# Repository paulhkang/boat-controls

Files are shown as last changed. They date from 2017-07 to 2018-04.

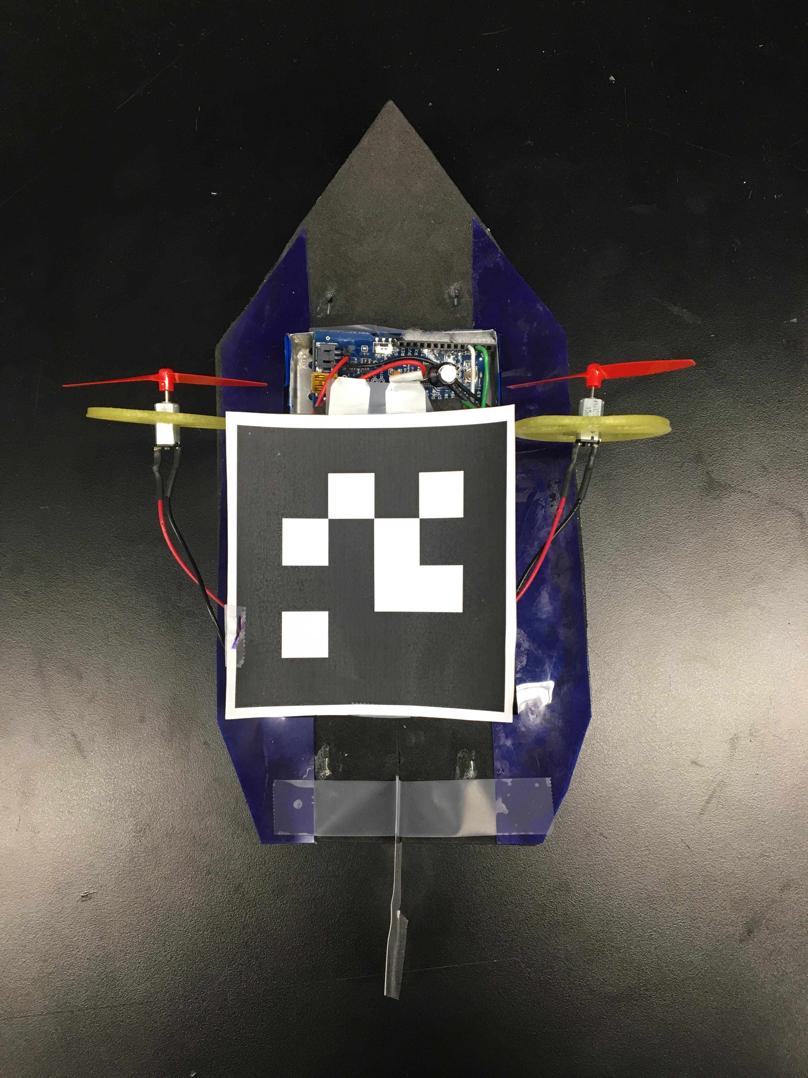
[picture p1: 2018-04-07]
Boat_Assembly/Photos/jack_boat_001.jpg

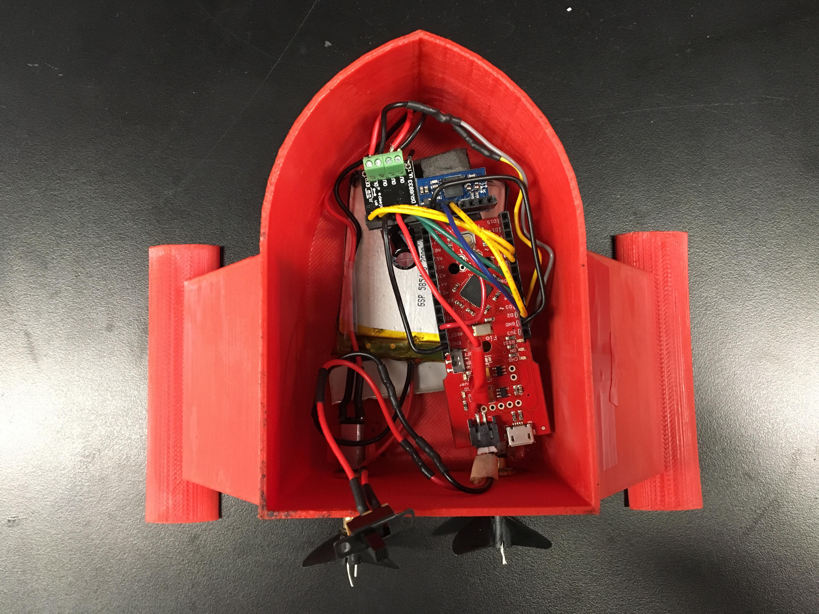
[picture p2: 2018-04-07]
Boat_Assembly/Photos/paul_boat_001.jpg

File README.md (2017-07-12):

# boat-controls
Controls for an Autonomous Boat

This repository contains the code for a control system on an autonomous boat.

The two contributors to this repository are Paul Kang and Rayhan Syed.
We are students at The Cooper Union, located in New York City.

The bno055.c and bno055.h files are used in reading from the Bosch Sensortec BNO055 sensor.
These files, as well as more detailed documentation on the software, can be found at: https://github.com/BoschSensortec/BNO055_driver.

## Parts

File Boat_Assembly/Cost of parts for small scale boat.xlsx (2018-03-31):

Part Name | Quantity | Cost | Link
P14350-ND motors | 2 | $4.11 | https://www.digikey.com/product-detail/en/nmb-technologies-corporation/PNN7RE08JD/P14350-ND/2417074
Arduino Fio | 1 | $24.95 | https://www.sparkfun.com/products/11520
Custom Arduino boards | 1 | $61.85 | X | (designed by Andrey Akhmetov, EE '20)
Li-Ion flat battery | 2 | 12.95 | https://www.sparkfun.com/products/8483
3D filament | As needed for testing
RC boat propellers | 3 (only 2 needed) | $7.98 | http://a.co/iIR0y6P
Total |  | $111.84
Non-costed parts:
Li-ion battery charger | 1
Brass motor shafts | 2 | Machined in-house (Sinisa Janjusevic)
Brass bearings | 2 | Machined in-house (Sinisa Janjusevic)
Vaseline for lubrication | N/A
Xbee S1 radio | 2 | https://www.sparkfun.com/products/8665
SparkFun Xbee Explorer Dongle | 1 | https://www.sparkfun.com/products/11697
Micro USB Cable (for writing to Arduino) | 1
Wire | N/A
Hot glue | N/A

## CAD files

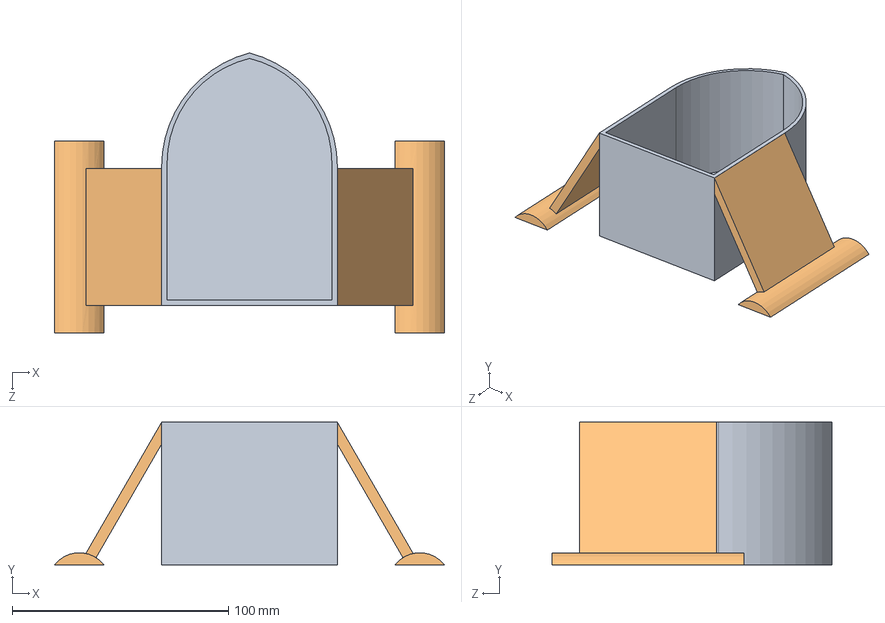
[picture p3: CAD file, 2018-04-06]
Boat_Assembly/CAD & Drawings/Boat Hull Assembly.SLDASM
180.3 x 66.0 x 129.5 mm
Boat Body
Boat Arm x 2

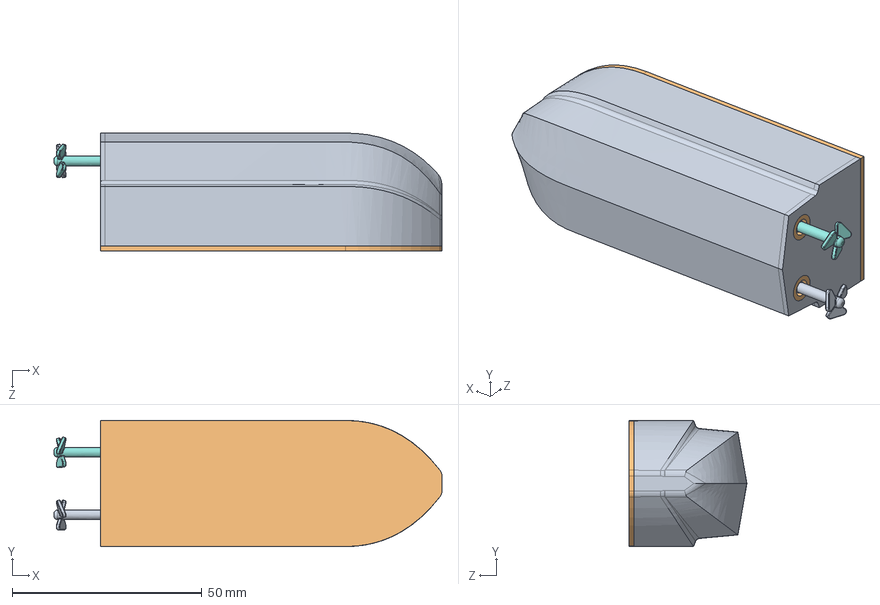
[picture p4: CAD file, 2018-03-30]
Boat_Assembly/TankData/mASV_CAD/dumb_boat.SLDASM
102.4 x 33.3 x 31.1 mm
hull
grommet x 2
battery_400mAh
miniBoard
XBee
minimotor_0615NS_sld x 2
minimotor_gearbox_4to1 x 2
propeller_LH
propeller_RH
cap

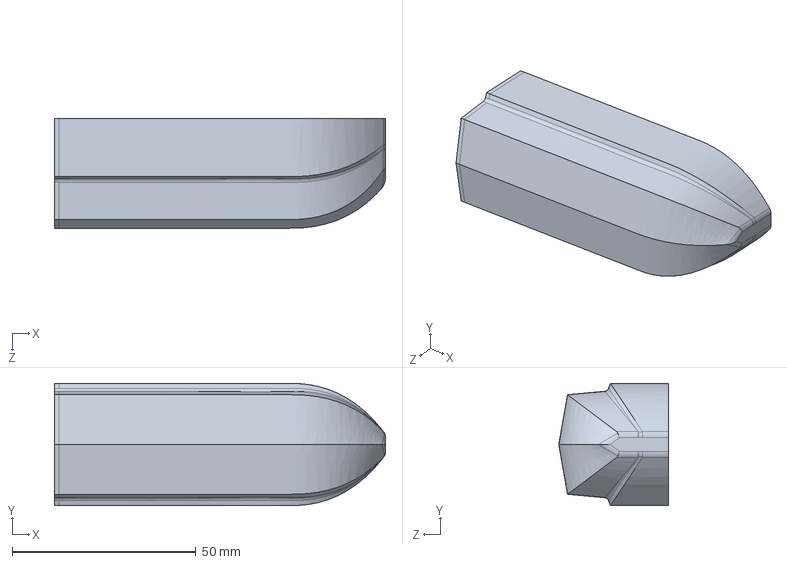
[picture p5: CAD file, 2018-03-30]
Boat_Assembly/TankData/mASV_CAD/hull.SLDPRT
90.2 x 33.3 x 29.8 mm

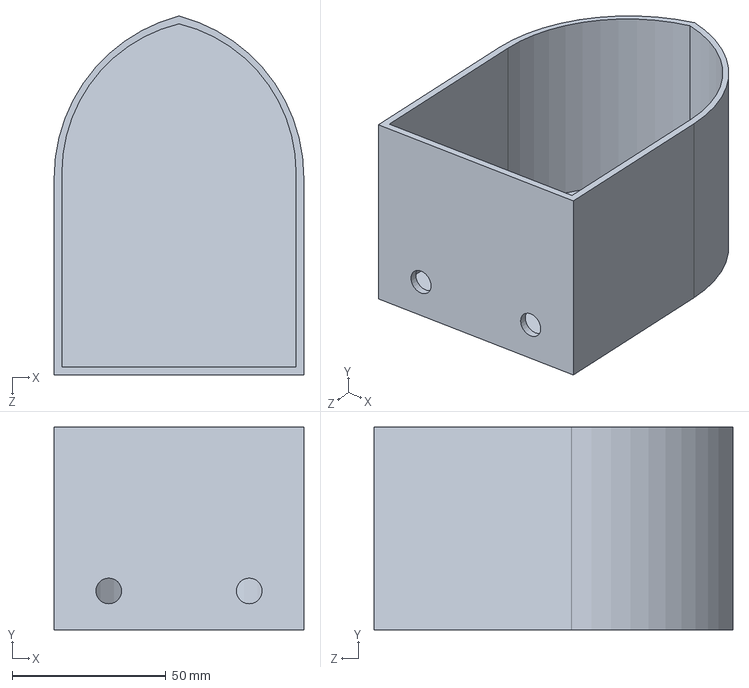
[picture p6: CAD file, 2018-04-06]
Boat_Assembly/CAD & Drawings/Boat Body.SLDPRT
81.3 x 66.0 x 116.8 mm

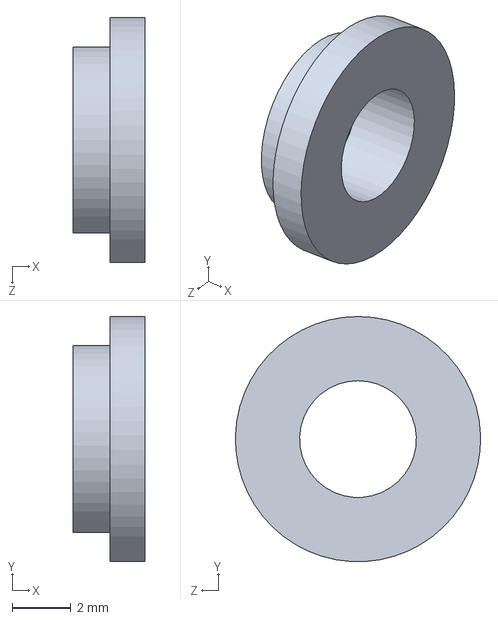
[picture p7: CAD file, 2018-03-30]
Boat_Assembly/TankData/mASV_CAD/grommet.SLDPRT
2.46 x 8.33 x 8.33 mm

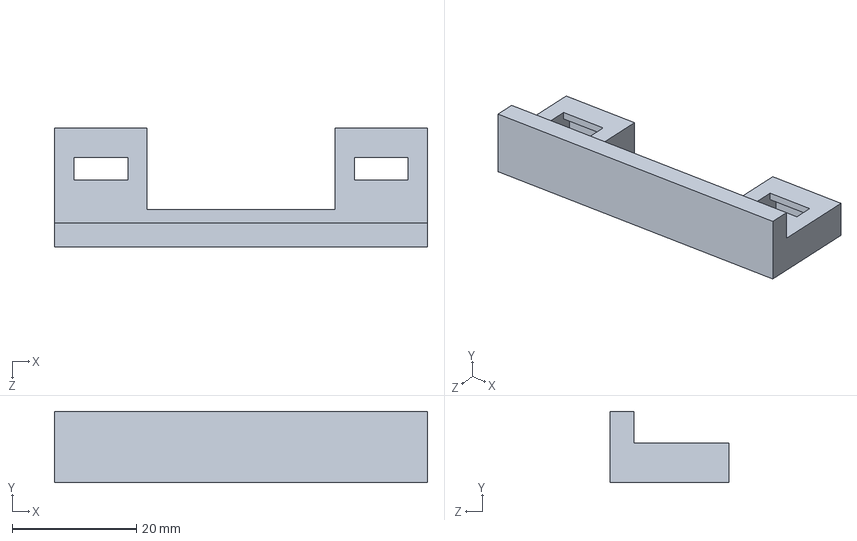
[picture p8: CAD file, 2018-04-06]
Boat_Assembly/CAD & Drawings/motor-mount.SLDPRT
59.9 x 11.4 x 19.0 mm

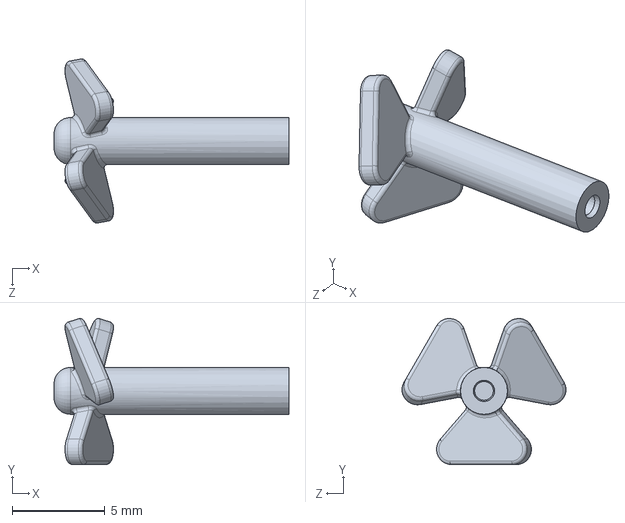
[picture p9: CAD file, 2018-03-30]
Boat_Assembly/TankData/mASV_CAD/propeller_RH.SLDPRT
12.7 x 7.89 x 8.87 mm

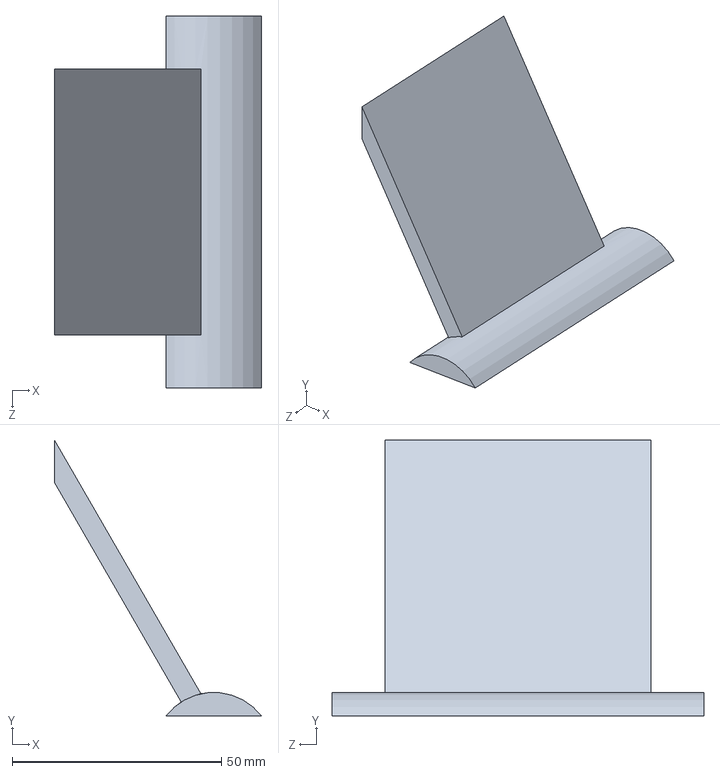
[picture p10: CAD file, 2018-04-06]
Boat_Assembly/CAD & Drawings/Boat Arm.SLDPRT
49.5 x 66.0 x 88.9 mm

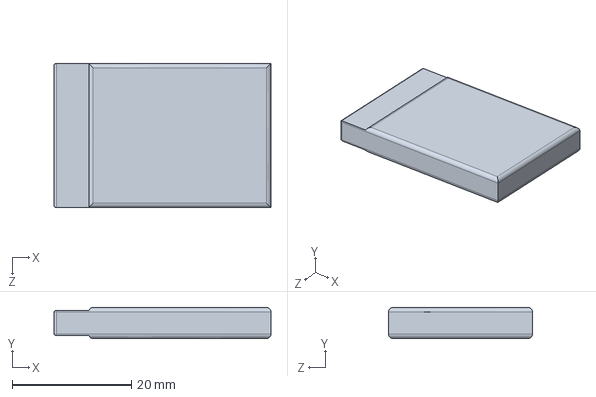
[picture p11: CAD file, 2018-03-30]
Boat_Assembly/TankData/mASV_CAD/battery_400mAh.SLDPRT
36.3 x 5.21 x 24.1 mm

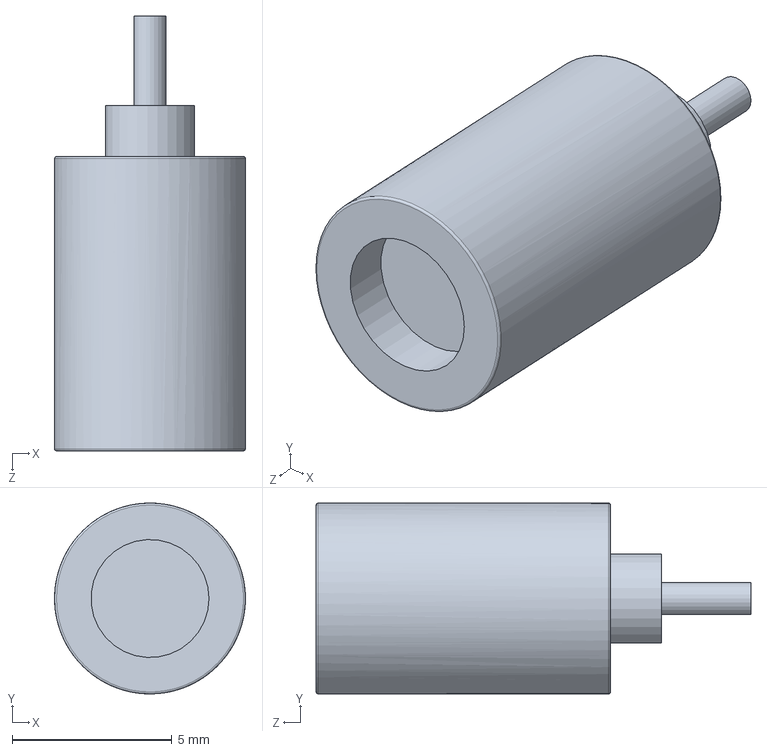
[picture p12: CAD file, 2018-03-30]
Boat_Assembly/TankData/mASV_CAD/minimotor_gearbox_4to1.SLDPRT
5.98 x 5.98 x 13.6 mm

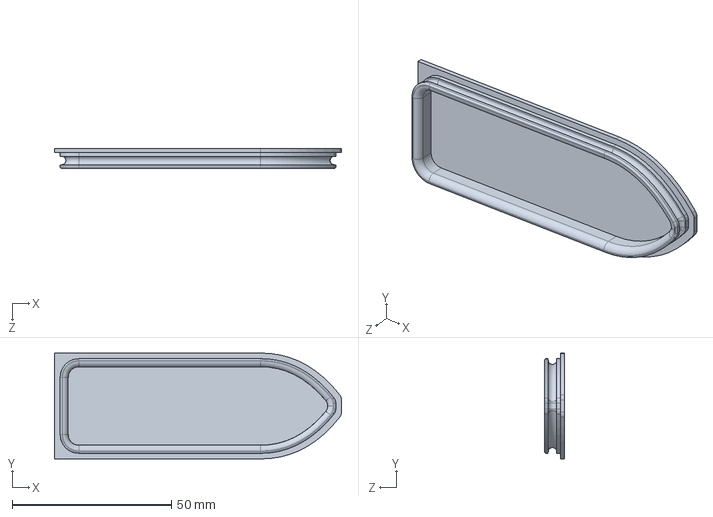
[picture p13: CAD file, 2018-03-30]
Boat_Assembly/TankData/mASV_CAD/cap.SLDPRT
90.2 x 33.3 x 6.35 mm

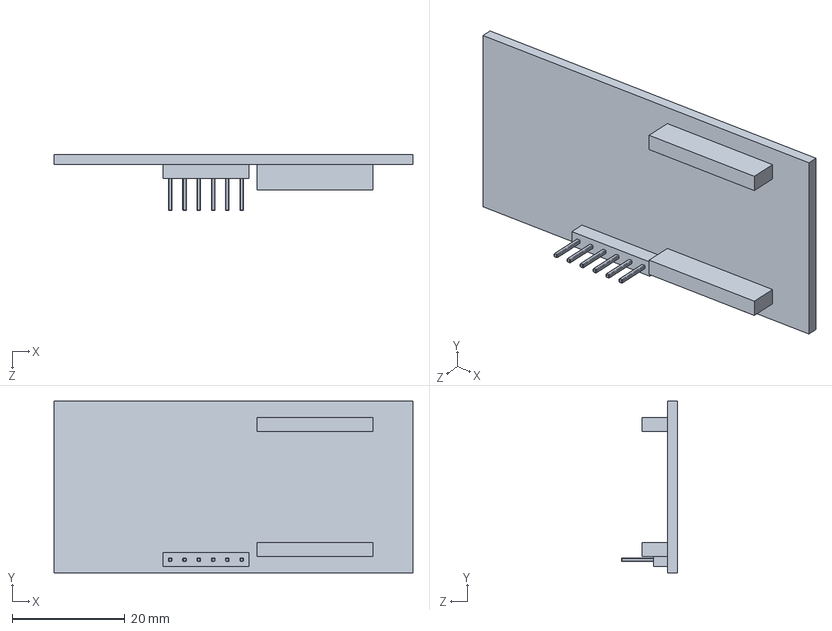
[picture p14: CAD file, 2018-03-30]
Boat_Assembly/TankData/mASV_CAD/miniBoard.SLDPRT
63.8 x 30.5 x 10.0 mm

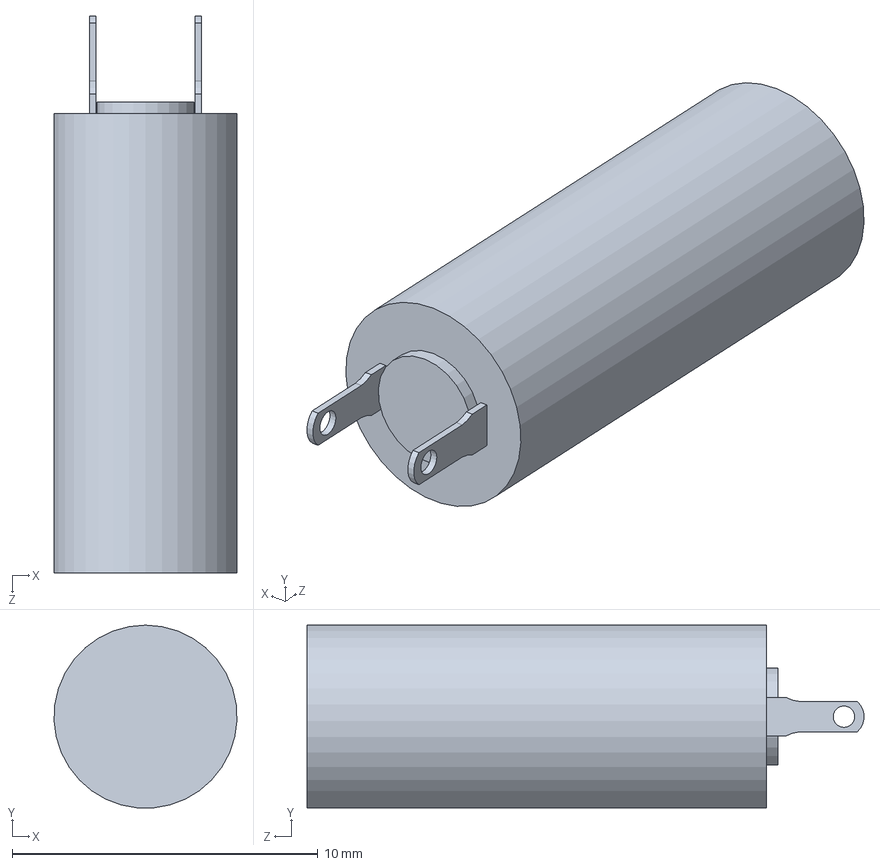
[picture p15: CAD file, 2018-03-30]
Boat_Assembly/TankData/mASV_CAD/minimotor_0615NS_sld.SLDPRT
5.99 x 5.98 x 18.2 mm

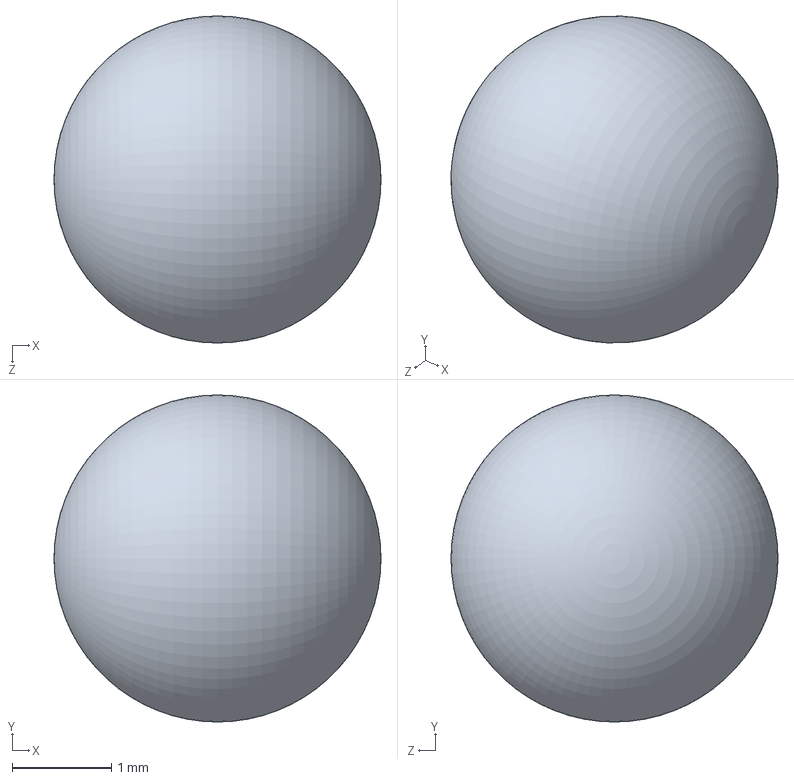
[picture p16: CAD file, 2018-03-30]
Boat_Assembly/TankData/mASV_CAD/lead_ball.SLDPRT
3.30 x 3.30 x 3.30 mm

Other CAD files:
Boat_Assembly/TankData/mASV_CAD/propeller_LH.SLDPRT
Boat_Assembly/TankData/mASV_CAD/XBee.SLDPRT
Boat_Assembly/CAD & Drawings/Boat Hull Assembly.SLDDRW
Boat_Assembly/CAD & Drawings/motor-mount.SLDDRW

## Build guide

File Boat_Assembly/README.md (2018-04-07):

# Boat_Assembly

This directory contains files used in the design/assembly of the boat. Files included are:

- Boat_Code3 (directory)

	This contains an Arduino file of the steering code for Jack Donnellan's boat. This code was written by Jack Donnellan and David Shekhtman. (as of 4/5/2018)

- Boat_Code3_Paul (directory)

	This contains an Arduino file of the steering code for the 3D-printed boat. This code was written by Jack Donnellan and David Shekhtman. (as of 4/5/2018)

- CAD & Drawings (directory)

	This directory includes CAD (SolidWorks) and drawing files of the boat hull and motor mount (initial version). These CAD files can be converted to .stl files and 3D-printed. Images of basic dimensioned drawings are also included.

- Photos (directory)

	Contains photos of Paul Kang and Jack Donnellan's boats.

- TankData (directory)

	This directory includes files from Dennis Larkin's thesis "An Experimental Testbed for Creating Controlled Lagrangian Coherent Structures", Drexel University, 2015. This thesis involved the creation of a similar boat for testing purposes. Files include Larkin's thesis, and CAD files of Larkin's boat. These files were useful in the design of our boat. Thanks to Dennis Larkin for providing these files.

- Cost of parts for small scale boat.xlsx

	An initial bill of materials for the boat. While this list contains all necessary components to construct the boat, any components that were later added are not included. The custom Arduino board was designed by Andrey Akhmetov, EE '20.

- Kang, Paul - Development of an Autonomous Boat.docx

	A description of the boat project, explaining the motivation behind and execution of the boat assembly. Contains explanations of design choices and boat systems.

- Waterproofing.docx

	A description of the motor alignment and waterproofing processes of the boat. These processes required a lot of troubleshooting.

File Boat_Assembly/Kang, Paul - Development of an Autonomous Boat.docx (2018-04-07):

Development of an Autonomous Boat

Paul Kang

The Cooper Union

B.E. M. Eng. ‘19

kang4@cooper.edu

Dirk Martin Luchtenburg

The Cooper Union

Advisor

dluchten@cooper.edu

Greg Caubel

The Cooper Union

B.E. M. Eng. ‘20

caubel2@cooper.edu

John Donnellan

The Cooper Union

M.E. ‘18

jackdonnellan161@gmail.com

David Shekhtman

The Cooper Union

M.E. ‘18

davshe98@gmail.com

David Shekhtman

The Cooper Union

M.E. ‘18

davshe98@gmail.com

Andrey Akhmetov

The Cooper Union

B.E. E. Eng. ‘20

hexafraction@gmail.com

Michael Lendino

The Cooper Union

B.E. E. Eng. ‘20

lending nbom@gmail.com

Aqib Sadique

The Cooper Union

B.E. M. Eng. ‘20

aqibsadique@gmail.com

Bhawanjot Shergill

The Cooper Union

B.E. E. Eng. ‘20

bhawanjonshergill@gmail.com

Rayhan Syed

The Cooper Union

B.E. E. Eng. ‘20

rsyed528@gmail.com

Abstract

As a continuation of a previous senior project completed at the Cooper Union, a boat with a 3D-printed hull and an Arduino-based controls system was designed and built. This boat was created as the beginning stage of an eventual planned fleet of autonomous, energy-efficient boats. Using an overhead-mounted camera, position and orientation of the boat are determined, and desired coordinates are sent to the boat via a wireless XBee radio. An on-board controls system propels the boat to these coordinates.

Introduction

A Cooper Union senior project carried out by Jack Donnellan, Sam Cavas, Sai Chikine, and Ryan Yun involved the creation of a system of energy efficient autonomous boats. [1] The project yielded a catamaran-style boat and operational camera-tracking software, as well as various flow field characterizations. This project aims to continue the work of Cavas et al, beginning with an improvement on the catamaran-style boat. The controls on this boat will then be refined such that the boat can be directed along known flow fields in an energy efficient manner. These flow fields were characterized by Cavas et al.

System Overview

The boat was 3D-printed out of PLA, and a custom Arduino shield was designed to work with a stock Sparkfun Arduino Fio v3. This Arduino shield provides functionality for powering the boat’s motors, as well as a gyroscope and accelerometer. The boat is propelled by 2 DC motors powered via pulse width modulation (PWM) signals from the Arduino. The Arduino control system is powered by a 3.7V rechargeable lithium polymer (LiPo) battery. A two-way XBee wireless communication system allows the boat and controlling laptop to communicate. During testing, the boat is placed in a circular indoor tank filled with water. An overhead camera is mounted on the ceiling above this tank. Through this camera, software tracks the live orientation and position of a marker image attached to the boat.

The figures below show the boat’s systems in more detail.

See Appendix for dimensioned drawing of boat hull CAD.

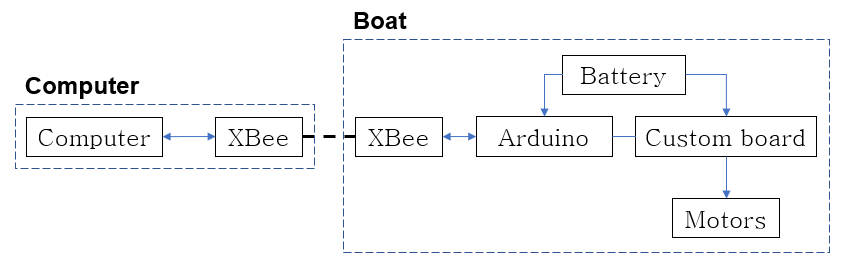
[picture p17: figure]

Figure 1. High-level block diagram of the boat parts. The dotted line between XBees indicates wireless communication.

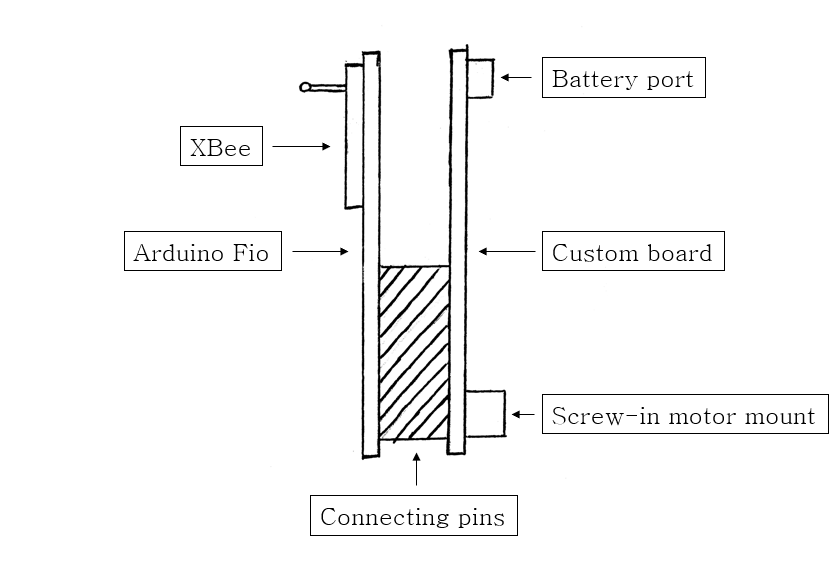
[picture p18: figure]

Figure 2. Side view of the main electronics of the boat. (wires and battery omitted)

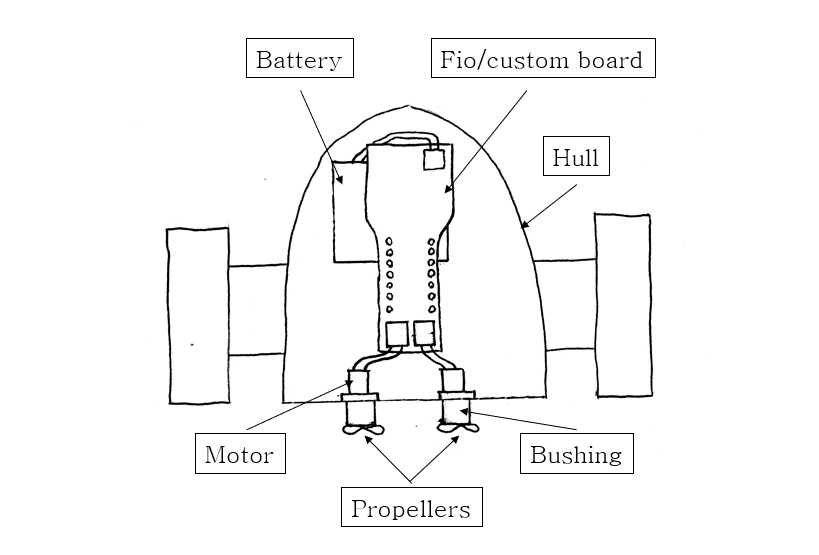
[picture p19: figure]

Figure 3. Top view of the boat.

Design Choices

Boat Hull

The main design parameters considered were size and weight, to maximize energy efficiency. A 3D-printed hull and LiPo battery were chosen to reduce weight, and the hull design was changed to be more space-efficient. Fins were added to both sides of the boat to prevent roll. As discussed in Cavas et al, the boat’s differential drive setup is more energy efficient than a propeller-rudder setup. The boat motors are held in place with 3D-printed PLA mounts, and motor shafts and bushings were machined out of brass. Two left-handed plastic RC boat propellers are attached to the motor shafts. In choosing propellers, the potential for propeller walk was not considered. Propeller walk may interfere with precise control over the boat; replacement of these propellers would be an improvement on this design. (see Conclusions) Vaseline is used to lubricate the motor shaft and provide waterproofing. (see Waterproofing.docx for more on waterproofing.)

Boat Electronics

The boat is controlled by a Sparkfun Arduino Fio v3, similar to the Arduino Fio used by Cavas et al. A custom Arduino shield was designed, which contains voltage regulators, a dual-H-bridge motor driver circuit, and a BNO055 sensor (9-axis gyroscope, accelerometer, and magnetometer). The Arduino sends PWM signals to the motor driver circuit, and the H-bridges allow each motor to be driven either forward or backward. The PWM signal allows for an effective voltage between 0 and 3.3V to be supplied to the motors. An XBee communications system consisting of two XBee radios allows for communication between the Arduino and a controlling laptop. One XBee radio is connected to the Arduino via a built-in port, and the other is connected to the laptop via a USB dongle. The laptop calculates desired coordinates and sends them wirelessly to the boat’s onboard Arduino control system. The Arduino then calculates the necessary changes in boat orientation and position, translates these changes into PWM signals, and sends these signals to the motors.

Conclusions

Currently, the boat is operational and can be controlled wirelessly from a laptop. Thus, the focus of this project is now the precision of this controllability. Future work includes calibration of the propulsion and coordinate tracking systems. Once the boat is fully controllable, the flow field experiments outlined in Cavas et al. will be used to generate energy-efficient trajectories. Further potential improvements to the boat design include refining or modifying hull design and replacing propellers to reduce propeller walk.

Acknowledgements

I would like to thank Professor Luchtenburg for his advice and tutelage. I would also like to thank David Shekhtman, Andrey Akhmetov, Jack Donnellan, Greg Caubel, Michael Lendino, Aqib Sadique, Bhawanjot Shergill, and Rayhan Syed for their work and help with the creation of this boat.

I would also like to thank Jack Donnellan, Sam Cavas, Sai Chikine, and Ryan Yun for their project, which laid the groundwork for this project.

References

[1] Cavas, S., Chikine, S., Donnellan, J., and Yun, R., 2017. “Energy Efficient Propulsion of Autonomous Boats”. The Cooper Union for the Advancement of Science and Art, New York, NY.

Appendix

Appendix A: Dimensioned Drawing of Boat Hull

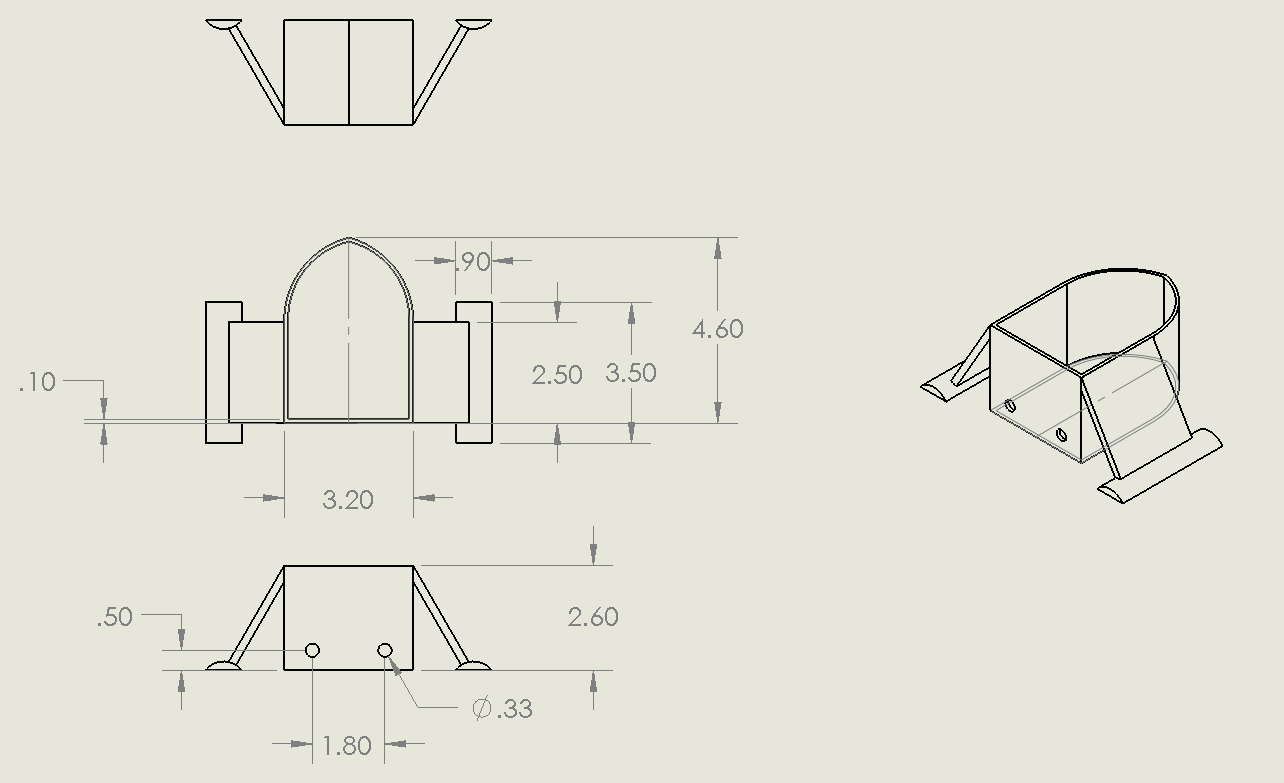
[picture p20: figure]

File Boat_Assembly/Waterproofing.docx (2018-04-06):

The motor alignment and waterproofing of this boat were more annoying than anticipated. This file documents our troubleshooting process for these two aspects of the boat.

Alignment

Motor alignment is crucial in allowing the motors to consistently spin. If the motor shafts are misaligned in their bushings, they will be finnicky and often not spin properly, causing motor burnout. However, it is also important that the motors are not constrained too tightly, as the viscous bearing effect allows the shaft to align itself as it rotates. So, the mounts must be solidly attached to the boat, but must allow for some movement of the motors.

Initially, one 3D-printed motor mount was used to mount both motors, as shown below (dimensions are in inches):

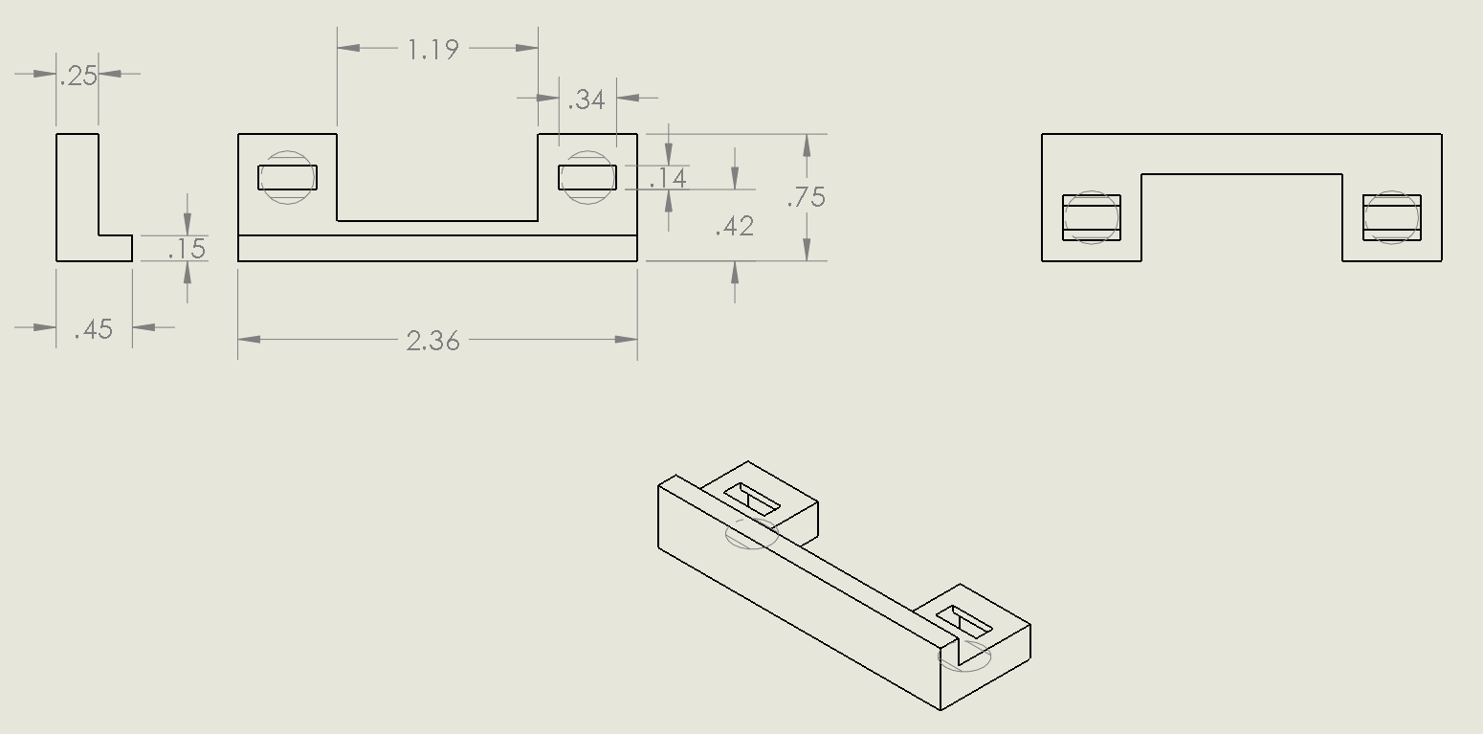
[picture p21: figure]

However, this mount proved to be problematic. Physically linking the two motors made it much more difficult to align both, as when one was aligned, the other was not. To fix this, we took the same mount design and simply 3D-printed the end parts: one for each motor. Each motor was then aligned separately, and its respective mount was glued to the boat hull.

Waterproofing

Waterproofing the boat was intertwined with shaft alignment because of the viscous bearing effect. Grease was used inside the bearings as a twofold measure: waterproofing the bearings and greasing the motor shaft. However, if the grease is too viscous, the motors cannot spin, and also cannot self-align through the viscous bearing effect.

Lucas Oil Marine Grease was found to be too viscous, so Vaseline was used instead. During waterproofing testing, we found that the bushing hugged the shaft too tightly, allowing any slight misalignment to prevent the motor from spinning. To fix this, we bore out the inside of the bushing, increasing the inner diameter by ~0.003”. More Vaseline was added to compensate for the larger hole.

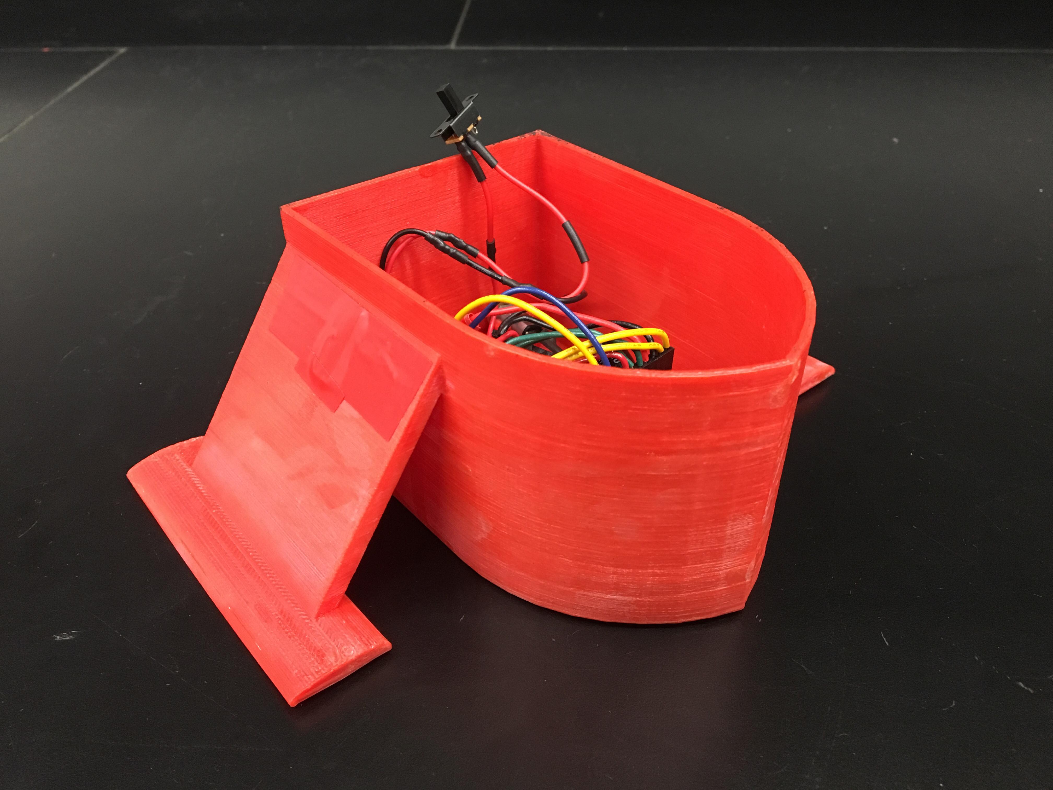
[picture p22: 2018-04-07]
Boat_Assembly/Photos/paul_boat_004.jpg

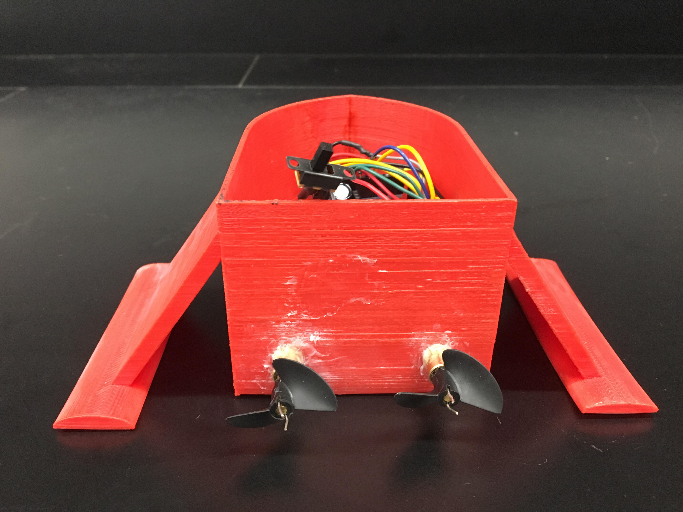
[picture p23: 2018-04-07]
Boat_Assembly/Photos/paul_boat_002.jpg

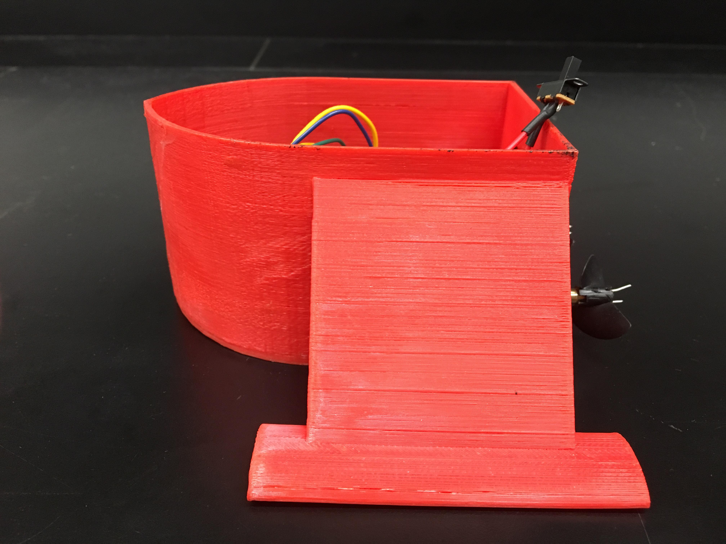
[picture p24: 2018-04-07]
Boat_Assembly/Photos/paul_boat_003.jpg

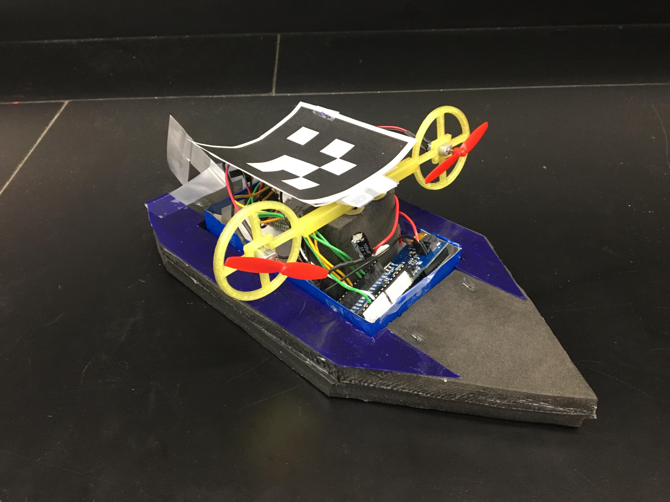
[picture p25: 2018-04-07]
Boat_Assembly/Photos/jack_boat_004.jpg

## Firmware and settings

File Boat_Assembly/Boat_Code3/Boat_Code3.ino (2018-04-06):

#include <Wire.h>
#include <Adafruit_Sensor.h>
#include <Adafruit_BNO055.h>
#include <utility/imumaths.h>
#include <SoftwareSerial.h>

//SoftwareSerial XBee(2, 3); // RX, TX
//StreamSend::sendObject(Serial, &charVariable, sizeof(charVariable));

//I^2C /Addresses
//#define MSTR_ADDR 0x24      //Master Address
//#define BCN_ADDR 0x16       //Beacon Address
#define CTRL_ADDR 0x11      //Motor Controller
#define GYR_ADDR 0x09       //Gyroscope Address

/* Set the delay between fresh samples */
#define BNO055_SAMPLERATE_DELAY_MS (25)
Adafruit_BNO055 bno = Adafruit_BNO055();

double offset=0.025;


float pos[5] = {0};  //x y Position Array of Boat
#define Xb pos[0]    //Current Boat X-coordinate
#define Yb pos[1]    //Current Boat Y-coordinate
#define theta_x2 pos[2]    //Current Boat Y-coordinate
#define dx pos[3]   //Start Point X-coordinate   //dx=x_ref-x_rel; x_ref=sqrt((y2-y1)*(y2-y1)+(x2-x1)*(x2-x1))+offset;//m Displacement between two waypoints (x1,y1) and (x2, y2)
#define theta_set pos[4]   //Start Point Y-coordinate //theta_set Desired Angle determined by waypoints (x1,y1) and (x2, y2)
double x_rel;        //Current Relative Position of Robot //x_rel=sqrt((yR-y1)*(yR-y1)+(xR-x1)*(xR-x1));//m Displacement of the Boat from the last waypoint (x1, y1)

//Left Motor
#define L0 4
//#define L1 7
#define LPWM 5  //enable

//Right Motor
#define R0 8
//#define R1 11
#define RPWM 9  //enable

#define pi 3.14159265359
double u_max=3.593*0.0254;//m/s @ 45RPM = 1*2*pi*(45rpm)*r_wheel/(60s/1min) Max Drive motor Speed @ 6V

float gain[3]={0.707,1.3836,0.5};
#define k_i_pos gain[0]
#define k_p_pos gain[1]
#define k_theta gain[2]

int v_lim=200;           //Speed Cap (Nonlinearity) Anti-Saturation Speed Cap 140 out of 255

//Prototypes
void StopMoving(int ctr1, int ctr2);             //designed specifically for locking drive motors
void MoveMotor(int dir, int pwm, int duty);    //designed specifically for drive motors
void getPos();
void pwm(int crt1,int duty);                                 //designed specifically for linear actuator and broom
int sign(double number);


void setup() {
  Serial.begin(57600);
  Wire.begin(CTRL_ADDR);
  /* Initialise the sensor */
  if(!bno.begin())
  {
    /* There was a problem detecting the BNO055 ... check your connections */
    Serial.print("Ooops, no BNO055 detected ... Check your wiring or I2C ADDR!");
    while(1);
  }

  delay(1000); 
  //Define Motor Pins as Outputs
  pinMode(L0, OUTPUT);//Direction
//  pinMode(L1, OUTPUT);//Direction
  pinMode(LPWM, OUTPUT);//Left PWM
  pinMode(R0, OUTPUT);//Direction
 // pinMode(R1, OUTPUT);//Direction
  pinMode(RPWM,OUTPUT);//Right PWM
}


int z = 0;

    
//IMU data initialization
double theta_x;
double theta_y;
double theta_z;
double d_theta; //Angular Deviation from desired orientation (rad) 


unsigned long time = 0;


/////////////////////////////////////////////////////////////////////////////////////////////////////////////////////////////////////////////
void loop() {
  
  if (z == 0) {
    time = 0;
    z=1;
    //Output Pin Initialization
    digitalWrite(L0,LOW);
    digitalWrite(LPWM,LOW);
    digitalWrite(R0,LOW);
    digitalWrite(RPWM,LOW);
    delay(5000);//5s break
  }
  /////////////////////////////////////////////////////////////////
  //define current time
  time = millis();
  
  
  //////////////////////////////////////////////////////////////////////////////////////////////
  //Read the Xbee
  
  //Read Sensors
  getPos();//Get Position and References from Camera and Central Computer
  //////////////////////////////////////////////////////////////////////////////////////////////
  //Read the IMU
  imu::Vector<3> euler = bno.getVector(Adafruit_BNO055::VECTOR_EULER);
  /* Display the floating point data */
  theta_x=2*pi-(euler.x())*pi/180;//put a neg. here to negate Body-fixed Z-axis
  theta_y=(euler.y())*pi/180;// Body-fixed x-axis
  theta_z=(euler.z())*pi/180;// Body-fixed y-axis 
  //IMU Acceleration Vector (No need.)
  //imu::Vector<3> acceler = bno.getVector(Adafruit_BNO055::VECTOR_ACCELEROMETER);
  //////////////////////////////////////////////////////////////////
  //Feedforward 2 points from a Curve (We are between 2 waypoints.)
  
  //Get differences between reference and current boat state in both orientation and displacement, respectively.
  d_theta = theta_diff(theta_x,theta_set);// Difference between Desired Angle and Current Boat Angle  //dx=x_ref-x_rel;//m is obtained from xbee.
  if(abs(d_theta)<(10*PI/180)){
    k_theta = 0.1;
  }
  else{
    k_theta = 0.3;
  }
  
  /////////////////////////////////////////////////////////////////////////////////////////////
  //Initialize Steering and Position Control Variables
  //Note that the critical idea is to avoid saturation of the actuator--> unusable actuator.
  double width=1.8125*0.0254;//m (45 - 46) mm distance between the two differential drive propeller axes
  int fL_st;                                                  //Left side steering control duty cycle
  int fR_st;                                                  //Right side steering control duty cycle
  int fL_pos;                                                 //Left side position control duty cycle
  int fR_pos;                                                 //Right side position control duty cycle
  ///////////////////////////////////////////////////////
  
  //Steering Control Laws (P-control)
  //Left Motor Control Law
  //Gains may need to be adjusted if one motor is faster (better) than another.
  fL_st=constrain((-floor(256*k_theta*(d_theta/u_max))),-18,18);
  //Right Motor Control Law
  fR_st=constrain((floor(256*k_theta*(d_theta/u_max))),-18,18);
  
//////////////////////////////////////////////////////////////  
  //Position Control Law (P-control)
  //Left Side Speed Control Law 
  fL_pos=constrain((floor(256*(k_p_pos*(dx)/u_max))),(-v_lim),v_lim);
  fR_pos=fL_pos;
  
  //Control Law Implentation
  MoveMotor(L0,LPWM,(fL_pos+fL_st));//Left Motor
  MoveMotor(R0,RPWM,(fR_pos+fR_st));//Right Motor
  
  //For Straight-Line testing purposes
  //MoveMotor(L0,L1,LPWM,(150+fL_st));//Left Motor 
  //MoveMotor(R0,R1,RPWM,(150+fR_st));//Right Motor

  /////////////////////////////////////////////////////////////////////////////////////////////
  //Debugging
  //Serial.print("Theta_Z: ");
  //Serial.println(theta_x);
  //Serial.print(" UL:   ");
  //Serial.print((fL_pos+fL_st));
  //Serial.print(",,,");
  //Serial.print(" UR: ");
  //Serial.print((fR_pos+fR_st));
  //Serial.println("");
  //Serial.print("dx:");
  //Serial.println(dx);  
  //Serial.print("d_theta:");
  //Serial.println(d_theta);
  delay(10);
  /////////////////////////////////////////////////////////////////////////////////////////////  
 
}
///////////////////////////////////////////////////////////////////////////////////////////////////////////////////////////////////////
//Motor Functions
void StopMoving(int ctr1, int ctr2){//Dead Stop
  digitalWrite(ctr1,LOW);
  digitalWrite(ctr2,LOW);  
}

void MoveMotor(int dir, int pwm, int duty){
  
  if (duty>0){//Move forward
    digitalWrite(dir,LOW);
    if (duty>255){
    digitalWrite(pwm,HIGH);
    }
    else{
    analogWrite(pwm,duty);
    }
  }
  else if(duty==0){//Smooth Stop
    digitalWrite(dir,LOW);
    digitalWrite(pwm,LOW);
  }
  else if(duty<0){//Move Backward
    digitalWrite(dir,HIGH);
    if (duty<-255){
    digitalWrite(pwm,LOW);
    }
    else{
    analogWrite(pwm,(255-abs(duty)));
    }
  }
  
  
}

void pwm(int ctr1,int duty){
  analogWrite(ctr1,duty);
}


int sign(double number) { return number<0 ? -1 : 1; }


////////////////////////////////////////////////////////////////////////////////////


////////////////////////////////////////////////////////////////////////////////////

//Calculate the difference in theta_z
double theta_diff(float thetax,double thetaset){
  double tole=0.05;
  double d_1=(thetaset-thetax);
  double d_2=(thetaset-thetax+2*pi);
  double d_3=(thetaset-thetax-2*pi);
  d_1=abs(d_1);
  d_2=abs(d_2);
  d_3=abs(d_3);
  
  //Minimize the difference in angle for continuity
  double dtheta=min(d_1,d_2);
  dtheta=min(dtheta,d_3);
  dtheta=abs(dtheta);
  //redefinition of d_theta
  double dth=0;
  if((dtheta<(d_1+tole))&&(dtheta>(d_1-tole))){
    dth=(thetaset-thetax);
  }
  else if((dtheta<(d_2+tole))&&(dtheta>(d_2-tole))) {
    dth=(2*pi+thetaset-thetax);
  }
  else if((dtheta<(d_3+tole))&&(dtheta>(d_3-tole))){
    dth=(thetaset-thetax-2*pi);
  }
  else{
    //do nothing
  }
  return(dth);
}


void getPos() {
  //read the XBee
  //https://stackoverflow.com/questions/14199279/reading-data-over-serial-arduino-and-xbee
  //https://arduino.stackexchange.com/questions/203/sending-large-amounts-of-serial-data
  int i=0;
  while(Serial.available() and i<5){ 
    pos[i++]= Serial.parseFloat();//get coordinate array x y
  }
}

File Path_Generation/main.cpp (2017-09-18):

#include <stdio.h>

void Action1();
void Action2();
int NoP;
struct Coordinates
{
    float X;
    float Y;
};
int main(void)
{
    printf("How many points are in the path that you want to travel? \n");
    scanf ("%d", &NoP);
    int a;
    while (1){
        printf("Choose the number of one of the following:\n");
        printf("1) Define parametrically \n");
        printf("2) Enter an array of data \n");
        printf("3) Exit program \n");
        scanf("%d", &a);
        switch(a) {
            case 1 :
                Action1();
                break;
            case 2 :
                Action2();
                break;
            case 3 :
                return 0;
            default :
                printf("Invalid choice\n" );
        }
    }
}
void Action1()
{
    float t;
    float t_upper;
    float t_lower;
    char X;
    char Y;
    float difference;
    printf("Define t's bounds, and X and Y in terms of t. \n");
    printf("What is the upper bound of t? \n");
    scanf("%f", &t_upper);
    printf("What is the lower bound of t? \n");
    scanf("%f", &t_lower);
    printf("What is X in terms of t? \n");
    scanf("%s", &X);
    printf("What is Y in terms of t? \n");
    scanf("%s", &Y);
    struct Coordinates array[NoP];
    difference = t_upper - t_lower;
    float increment;
    increment = difference/(NoP-1);
    t = t_lower;
    int n;
    for(n=0; t <= t_upper; t= t + increment, n++){
        array[n].X = X;
        array[n].Y = Y;
        printf ("%f \n", t);
    }
    int i;
    int b;
    printf("\n\n Here is the resulting table:\n\n");
    for (i = 0; i < n; i++) {
        printf("X = %0.3f\t Y = %0.3f", array[i].X, array[i].Y);
        printf("\n");
    }
    printf("would you like to save this to a file? Enter the corresponding number.\n");
    printf("1) Yes \n");
    printf("2) No, I want to start over. \n");
    printf("3) Return to main menu. \n");
    scanf("%d", &b);
    switch(b) {
        case 1 :
        {
            FILE *file;
            file = fopen("Parametric_Path.txt", "wb");
            char* base = (char*) array;
            for(int j = 0; j < sizeof(array); j++){
                fputc(*(base+j), file);
            }
            fclose(file);
        }
            break;
        case 2 :
            Action1();
            break;
        case 3 :
            break;
        default :
            printf("Invalid choice\n" );
            Action1 ();
    }
}
void Action2() {
    int b;
    struct Coordinates array[NoP];
    printf("Enter the X coordinates in the table in increasing fashion. \n");
    int i;
    for (i = 0; i < NoP; i++) {
        scanf("%f", &array[i].X );
    }
    printf("Enter the Y coordinates in the order that corresponds to the order X's were entered. \n");
    for (i = 0; i < NoP; i++) {
        scanf("%f", &array[i].Y );
    }
    printf("\n\n Here are the values you entered:\n\n");
    for (i = 0; i < NoP; i++) {
        printf("X = %0.3f\t Y = %0.3f", array[i].X , array[i].Y );
        printf("\n");
    }
    printf("would you like to save this to a file? Enter the corresponding number.\n");
    printf("1) Yes \n");
    printf("2) No, I want to start over. \n");
    printf("3) Return to main menu. \n");
    scanf("%d", &b);
    switch(b) {
        case 1 :
        {
            FILE *file;
            file = fopen("Data_Array_Path.txt", "wb");
            char* base = (char*) array;
            for(int j = 0; j < sizeof(array); j++){
                fputc(*(base+j), file);
            }
            fclose(file);
        }
            break;
        case 2 :
            Action2();
            break;
        case 3 :
            break;
        default :
            printf("Invalid choice\n" );
            Action2 ();
    }
}

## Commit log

2018-03-30 Created Boat_Assembly
    [XBee.SLDPRT, battery_400mAh.SLDPRT, cap.SLDPRT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]
2018-03-31 Added BOM and technical report, edited readme
    [Cost of parts for small scale boat.xlsx]
2018-04-06 Added steering code, CAD & drawings, waterproofing documentation. Updated writeup and readme.
    [Boat Arm.SLDPRT, Boat Body.SLDPRT, Boat Hull Assembly.SLDASM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]
